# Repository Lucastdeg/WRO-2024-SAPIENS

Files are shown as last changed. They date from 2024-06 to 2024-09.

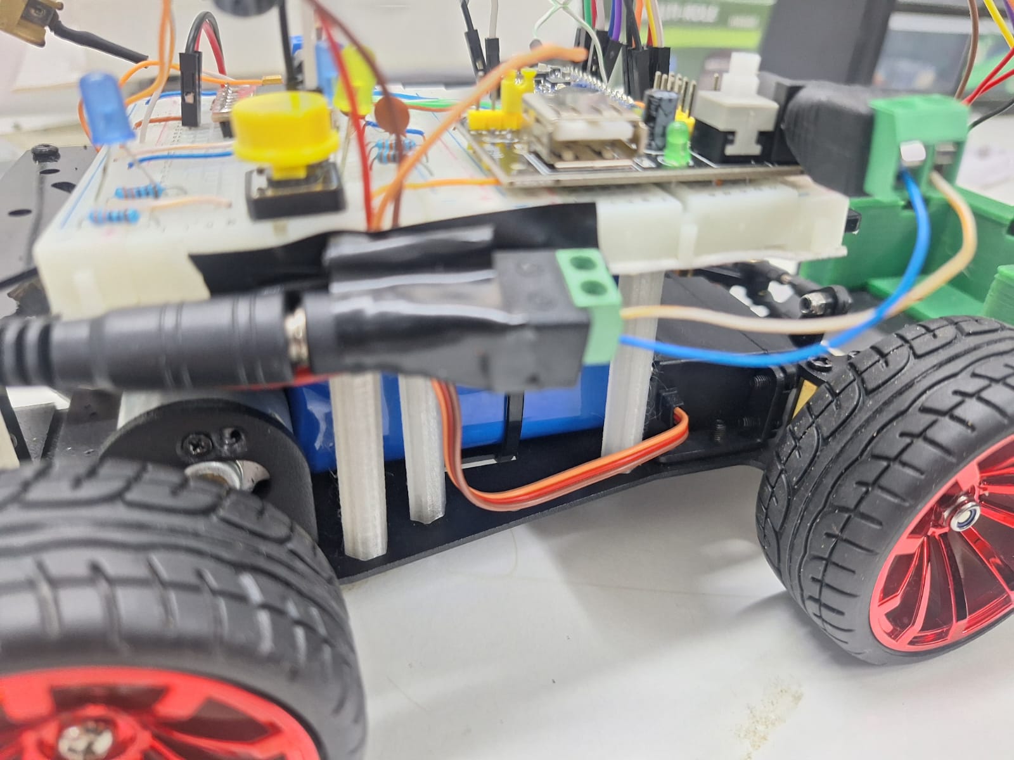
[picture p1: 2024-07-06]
v-photos/Electromechanical_Components/Battery Connection to circuit (Male Outing).jpeg

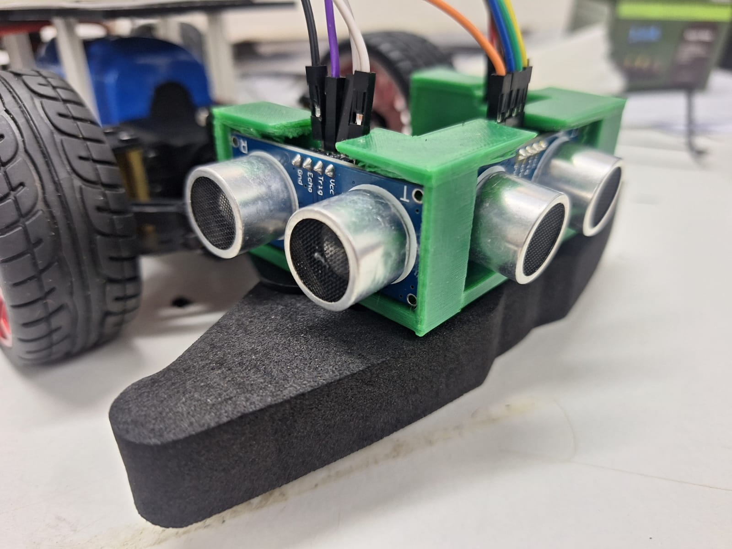
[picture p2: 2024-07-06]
v-photos/Electromechanical_Components/The Ultrasonic Sensors.jpeg

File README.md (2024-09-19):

# WRO-2024-SAPIENS
WRO-2024-SAPIENS

## Engineering Materials
All the materials used to create our robot
- 1 Arduino Nano Every (https://docs.arduino.cc/hardware/nano-every/)
- 1 TB6612 H-Bridge (HW-166)
- 4 Ultrasonic Sensors (1 at the front, 1 at the back, the other two right and left)
- 1 Small on/off switch
- 1 PushButton
- 1 Blue LEDS (1 for power, one for indication of the code)
- 2 resistors (360 Ohms) for code Indicator LEDS
- 25 Proto Wires
- 34 Rigid Wires (Hand cut)
- 2 Big Rigid Wires
- 2 Ceramic Capacitor 104
- 1 Capacitor 100 25-50V
- 1 Voltage Regulator L7805
- 1 Mini Power Supply HW-131 (Also works as voltage regulator) 5V and 3.3V2
- 1 Porta Fusibles
- 12V Battery 3S (18650 + BMS + 2 cable outings) (more about this can be seen in the electromehcanical components)
- 1 Chasis (DC Auto) This includes:
    - 4 Wheels
    - 1 Motor (more about this explained in other sections)
    - 1 Servo
- Multiple 3d pieces whih can be found in the following directory
[3d_files](models/3D_files/)



## Building instructions
- Chasis (Motors and base): https://mp.weixin.qq.com/s/dOADMsXeo7Lxebgg0yiY5Q
- Electronics (Circuit and battery): [The circuit diagram can be found in the schemes directory](schemes/)
- Code (For the arduino): [The source code can be found in the src directory](src/)

## Contents
- [Models](models/) This directory contains all used 3d models
- [Other](other/) This directory is empty for now, as no miscellancious files have had to be added
- [Process](process/) This directory will be completed for the national as it will contain the process that it took for us to get there
- [Schemes](schemes/) All wiring diagrams can be found in this directory
- [Source Code](src/) This directory contains all the code used in this proyect
- [Team Photos](t-photos/) The official Team photos can be found here
- [Performance Videos](p-videos/) The robot Performance videos for each challenge
- [Vehicle Pictures](v-photos/) All vehicle photos can be found in this directory, including some individual components
This is just a test to see if content linking works

## Introduction
Brief intro on our solution

For our robotics competition, we developed an innovative navigation solution that leverages Arduino's vision capabilities to detect and respond to color signals. By utilizing a camera module, our robot can identify green and red colors, which dictate its turning directions—left for green and right for red. This color-based navigation system is complemented by a comprehensive obstacle detection and avoidance mechanism.

To enhance our robot's awareness and maneuverability, we integrated four ultrasonic sensors—three positioned at the front and one at the back. These sensors provide real-time distance measurements, enabling the robot to detect and avoid obstacles from multiple directions. Our approach demonstrates the synergy of vision technology, ultrasonic sensing, and precise control algorithms, resulting in a responsive and reliable robotic solution.



## Mobility 
Our robot uses an Ackerman steering system, with this steering system we can make our robot do the turns that have to be done during the 3 rounds. But because of the shape of our chassis and the type of steering system we use, our robot can only turn up to a certain point. In the case of turning to the right, it can only turn 30 degrees and in the left one it can only turn 10 degrees.

Here you can see the shape of the chassis of our robot as a guide:
- [Chassis of our robot](v-photos/) 



Some of the problems we faced with the steering system is that we had to come up with a way for the robot to make the turns neither too tight nor too wide, to fix this we use ultrasonic sensors on the front, right and left side of the front of the robot that are detecting how far it started and how many degrees it has to move forward while it is turning. For example during the open challenge round we made the robot turn when one of the ultrasonic sensors on one of the sides stops detecting or detects a greater distance than it had detected during the straight line, the sensor that performs this action depends on whether it is the one on the right or left, when it is the one on the right is when the round is being performed clockwise and when it is the one on the left when it is counterclockwise. 

Meanwhile the servo motor is at 80 degrees the robot will turn to the left, so if it is at 120 degrees the robot will turn to the right, but you think that when the servo motor is at 100 degrees it will be in a position in which the wheels will be straight, this thought is incorrect because when the servo is at 100 degrees it will be slightly turning to the right, then we ask two questions, the first one is: So how many degrees should be the servo motor so that the robot wheels are straight? To answer this question, the degrees that the servo must be at for the wheels to be straight is 90 degrees, and this is where the second question comes in, which is: Why when the servo is at 90 degrees will the wheels be straight, if when the servo was at 80 degrees the robot would turn to the left and when the servo was at 120 degrees the robot would turn to the right, if the degrees that are in between these two numbers of degrees are 100 degrees? Well to answer this question, the 90 degree position is considered "straight" or "neutral" in many servo motor systems because it is the preconfigured standard in many servos to indicate that there is no deviation to the left or right and because of how we have the servo positioned with the chassis we are using and the Ackerman steering system our steering only goes from 80 to 120 degrees.

For the speed management part, our robot is generally going to go at 120 speed on straight lines, while it is rotating it will go at 100 of speed.

As for the equations we use 2 formulas, between the 2 formulas we have the turning time, this establishes that the speed that we are using during the turn, that is 100 We are going to divide it by 100 and the result we are going to multiply it by 1200 and this would give us the time during which we are going to rotate in milliseconds; the second formula is about the angle of rotation in this we are going to divide the speed by the result of the previous formula, then this result we are going to multiply it by 130 and the result that this formula gives us we are going to subtract it to another 130 and the result of this subtraction is going to give us the angle with which we are going to rotate. We use these formulas to make the turns between sections. 

## Strategy
Strategy Explanation
Color Detection with Arduino:
We integrated a Nicla vision with the arduino nano every to accurately detect colors. This system allows the robot to recognize green and red colors, which serve as signals to turn left or right, respectively. By using a camera module and appropriate color detection algorithms, the robot can continuously monitor its environment and respond in real time.

Directional Decision Making:
Upon detecting the color green, the robot is programmed to turn left. Conversely, when red is detected, the robot turns right. This color-based decision-making process ensures that the robot navigates efficiently and avoids obstacles or follows a designated path based on the predefined color signals.

Border Detection and Turning:
In addition to color detection, our robot is equipped with ultrasonic sensors to identify when and where it should turn. It uses an "umbral" which is a certain distance which if the robot pases, it will start to turn to a certain direction. That direction is decided by the other two ultrasonic sensors to the left and to the right.

Implementation Details
Code and Integration:
Our code, available here, outlines the specific algorithms and logic used for color detection, decision-making, and obstacle avoidance. The integration of the vision system with Arduino's control mechanisms is crucial for the robot's functionality.

Color Detection Algorithm:
The algorithm processes the camera feed to identify the presence of green or red. This involves filtering the image to isolate these colors and then using thresholding techniques to determine the direction.



Obstacle Avoidance Routine:
When the sensors detect an obstacle, the robot executes a series of steps to navigate around it. This includes stopping, scanning the surroundings, calculating an alternate path, and resuming its movement while continuing to rely on the color signals for direction.

Conclusion
Our solution leverages the capabilities of Arduino's vision system to create a responsive and efficient navigation strategy. By combining color detection with obstacle avoidance, our robot can intelligently navigate its environment, making it well-suited for the challenges of the competition.

This approach not only demonstrates the effectiveness of integrating vision with control systems but also highlights the importance of robust algorithms in achieving reliable performance in dynamic conditions.

## Code Explanation
In order to enact our strategy and enable our robot to complete each phase, our team created multiple programs that will be summarized and explained in the following text. For reference look at the [src directory](src).

The src directory is divided into 3 sections, Arduino Code, Nicla Code, and Other. This text will focus on the Arduino code as the Nicla is currently not being used. [The Arduino Code Directory](src/Arduino Code/) is divided in 2 sections, phase 1 and phase 2. At the time of writing, only phase 1 has been completed, that being said, our proyect is still in development, and in the near future it will be added to the github. 

[Phase 1](src/Arduino_Code/Phase_1):
Phase 1 contains multiple programs to show how our code has changed, the main code is called newcodephase1

- The program starts by defining all variables and importing all libraries, this include, all pins (except the two Led indicators), the max angle for the servo, and some other useful variables.

- Next is the PD, or Proportional Derivative. This PD is used later in "Accelerar Recto" to help mantain the robot in a straight line, there are multiple comments in the code explaining the PD, so the specific details will not be mentioned in this text. 

- After this comes the set up function, which as is said in the name, sets up the robot. It defines all pin modes and the servo. 

- Then comes the actual main part of the code, which can be found in the loop function. The loop function starts with a while loop that will repeat until a button is pressed. Pin #5 is in mode Input, which means that it recieves current. When the button is pressed, current from the battery is passed into the pin which causes the while loop to end. After the while loop ends, the 3 ultrasonic sensors measure the current distance, and each value is defined in a variable. This is done by calling the "medir_distancia" function which returns a float value.
  
- The medir distancia function can be found in line 241, it uses "cases" to determine which ultrasonic has to be activated. Once that is defined, the ultrasonic sends the sound waves and a duration value is returned, this value is processed by using the formula ((duration * 0.034 / 2)*0.95), which returns a distance reading in centimeters.

- Returning to the loop function, next up, a for loop starts. This for loop repeats 70 times, which is an absurd number of times right? Well thats the amount of times the function we use has to repeat in order to complete the 3 laps. Unfortunately, this is due to a weird error in our code that makes it so sometimes the turn function ends prematurely. 70 loops garantues that the robot completes the 3 laps, but in exchange, sometimes it does 3.5 or 4 laps, which means we can't consistently stop in the initial spot (this subtracts 3 points from our phase 1 score)

- Getting back to the functions used, first_turn is the function used for all turns, it was supposed to be only a function for the first turn, but it was so consistent we just used it repeatedly. First_turn is made up of 2 main parts, moving the robot forwards until it meets the umbral (or the left/right sensor detect more than 150 cms which indicated a turn), and then the actual turning.
- When the robot goes forward our pd constantly corrects the robot's position, we also have save crash function which makes it so if the robot is about to crash, it goes backwards and turns, preventing it from ending the round. This repeats until, how we mentioned earlier, the ultrasonic sensors forwards and back match the umbral or the right/left sensors detect more than 150 cms. It should probably be noted that the left anf right sensors almost never end the loop, and it is almost always the umbral.
- After the forwards loop ends, the robot detects right and left to decide what direction it will turn, the function left_turn and right_turn take in 2 parameters. Angle and time, angle being the angle at which it will turn, and time being the amount of time it will turn. Yet, if you see the actual code, you will notice that we set time at 0, so that means it shouldn't be turning right? Well, we found out that turning bya time was very inconsistent since gradual errors make the robot eventually crash, for this reason we are now using the left_end_turn function, which is incredibly consistent for 2 main reasons
- 1. It turns gradually from the specified angle (normally 60) to 84, increasing 1 degree every 112 miliseconds
  2. It turns, not by time, but until the ultrasonic sensors detect from a range of 100 to 30. This is the main reason why the robot is so consistent when turning compared to the previous code. Before, some very small errors could lead to crashes by the second lap, but with this code, we decrease the effect of those small errors substantially, since every turn will always be mostly straight, no matter at what angle it starts.

 - When the for loop ends, the breaking function (whichs stops the robot) sets in and the robot stops.

[Phase 2](src/):
Phase 2 consists of two different programs, one for the arduino nano every, and one for the nicla vision. Check each of their respective directories to see the code. The code for the nicla vision will be covered first, it focuses primarily on the color detection, but it also has the necessary integration modules to pass the information onto the nano every.

First of all let's cover the integration:
- The integration uses the wire library to connect the Nicla Vision and Nano every. It connects them bya I2C, or SCl and SDA connection. In both programs, the baudrate is set to 100000 and the address is set to the number 8. In the code it can be seen how the Nicla Vision is set to be the slave, this means that the nicla vision will send information to the nano every when it is called, if it was the other way around (like it previously was) the nano every would be called by the nicla vision.

Next is the color detection:
- The nicla vision will send 0 to the arduino nano every if it is green and 1 if it is red. It detects the colors by using the blob function integrated into openmv. The blob function contains parameters to define the sensitivity of the detection. It is based on the pixel count, the pixel area count and the intensity of the color. Two lists of different types of green and red are supplied to the function so that the camera can identify the color it is looking for. To determine the color that is going to be sent, the areas of all the detected blobs are added for red and for green. The one with the largest amount of area (the biggest amount of pixels) is the one the robot detects. Now, sometimes there will be no blocks in front of the robot, to detect this, we set a lower boundary of around 400 pixels, so if the total area is less than 400, no colors will be sent back to the robot.

Now, how do we utilize the 0s and 1s that we will recieve from the nicla vision?
For that we need to undertsand the arduino nano every's code:
- The code for phase 2 is vaguely based off of the code for phase 1, it uses a similar turn that measures the length of both ultrasonic sensors, the difference is it has an initial turn based on time. Besides from that it uses 2 functions to dodge left and right based on the readings of ultrasonic sensors. Before that though, it has to detect the color thats in front of the robot, it does this by calling the nicla vision and defining a variable as 0 or 1, (if there is no color it gets defined as 2). Then it dodges left or right depending on the reading and after that it will start going in alternating directions, by that it means if it detects red initially, it will go green next, and then red, alternating (as this pattern will always be present).

- This repeats until the robot crashes as we unfortunately, did not have time to do phase 3.

## Electromechanical Components
A lithium battery pack is being used in 3S1P configuration where 2 batteries are in parallel and then this pack is in series with the 2 batteries, to give a total of 12.6 Volts with 1900mAh capacity, together with the help of a BMS to manage the power input and output.
From this battery pack we are getting two cables, of which one has a male terminal and the other has a female terminal.

4 ultrasonic arduino sensors HC-SRO4 are being used. This sensor provides 2cm to 400cm of non-contact measurement functionality with a ranging accuracy that can reach up to 3mm. Each HC-SR04 module includes an ultrasonic transmitter, a receiver and a control circuit. There are only four pins that you need to worry about on the HC-SR04: VCC (Power), Trig (Trigger), Echo (Receive), and GND (Ground).

We used a Nicla Vision to detect the color of the obstacles, we made an algorithm to give the robot the ability to differentiate between green and red. 
We connected the Nicla Vision with the Arduino Nano Every through the SCL and SDA signals. 
When the Nicla Vision passes the information to the arduino about the color of the obstacle the arduino processes it and decides to turn left or right depending on whether the obstacle is red or green. 

Here is how the components are connected:
- [Wiring Diagrams](schemes/)

Unfortunately the Nicla Vision we used could not be found or obtained in the application we used for this reason we could not include it in the wiring diagram. But here is how the Nicla Vision is connected to the Arduino Nano Every:
-SDA from the Nicla Vision to pin D18 (SDA) of the Nano Every.
-SCL from the Nicla Vision to the D19 pin (SCL) of the Nano Every
-GND from the Nicla Vision to GND of the Nano Every
-VIN from the Nicla Vision to the 5V+ pin of the Nano Every

Here are some pictures of the batteries and sensors that we use: 
- [Batteries](v-photos/Electromechanical_Components/)

## Power Management
The battery power is separated in two parts. 
One part feeds the Arduino Nano Every and the Ultrasonic Sensors with 5 volts. This part make use of the Mini Power Supply HW-131 to regulate the voltage. 
The other part feeds the H-Bride TB6612 with 12 volts. 
Of course, all grounds are connected, but the 12 volts are only supplied in one positive line, this is the line that feeds the H-Bridge. 
Yet, this line connects to another positive line, but with the L7805 voltage regulator. This voltage regulator ensures that the servo and the power LED get 5 volts. Finally, the servo uses a capacitor to store energy in the case that the current demand is too high.

""Note: We use a porta fusible for safety of a short circuit in the 12 volts outing. It is highly recomended that this is used as this lithium battery could lead to a very dangerous safety hazard if not managed carefully. 

- [You can see the vehicle picture for reference](v-photos/)

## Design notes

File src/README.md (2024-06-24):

# Source Code
This directory contains all the code used for our completion of the 2024 Future Engineers challenge

It is separated into three main directories:
Arduino Code - contains the code used for the arduino nano every
Nicla Vision Code - contains the code used for the nicla vision
Other - miscellaneous programs used for the development of our solution (such as the PID simulator created using python)

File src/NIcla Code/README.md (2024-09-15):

# Nicla Vision Code

The code is explained in the main readme file. 

Just for you though, Ill vaguely explain it here as well
The code consists of one main function and inside of that there are multiple functions

- cameraConfig is a higher order function that sets up the camera and takes a picture 
- •	find_color_blobs gets the amount of pixels in a all color blobs and sends back 0 for green or 1 for red, depending on how many pixels are found for each color.
- Send info simply sends a value, (0 or 1) to the specified address
- I recommend greatly that you look at the code, there are multiple comments that get into more detail on the integration

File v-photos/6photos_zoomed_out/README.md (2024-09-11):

# 6 Photos

These photos include the nicla vision and some other minor change that were made to the robot
- Ultrasonic sensor in the back
- The new cables for the battery connection
- Changed position of capacitator
- Nicla Vision (disconnected)
- Changed Blue Led
- New button
- Not using Tape for 5v outing anymore
- New Servo
- New ultrasonic sensors
- Foam at front to protect robot from crashes

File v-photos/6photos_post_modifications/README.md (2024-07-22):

# Vehicle Pictures Post Modifications

While practicing over the week our team encountered multiple problems
1. The rigid cables were burnt and were not transmitting voltage/current well
2. The on/off switch had the same problem (although the reason is still only a theory)
3. The Battery was not charging
4. The Voltage regulator was not working

Due to this we had to change multiple things on the robot that can be seen in the new pictures

- We changed the battery so you might notice there are different cables for the battery now (the zip tie is also different)
- We changed the rigid cables to thicker bigger cables that could handle more voltage/current
- We replaced the voltage regulator
- We changed the on/off switch (you can see the zip tie is different)

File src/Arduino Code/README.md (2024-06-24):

# Arduino Code

All the code used for the arduino nano every
Contains:
Mention contents

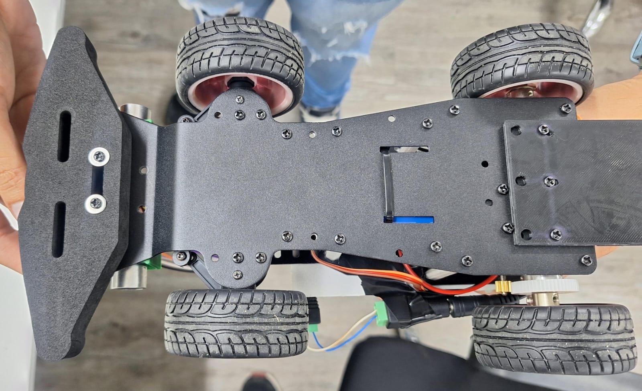
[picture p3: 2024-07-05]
v-photos/6photos_pre_modifications/Bottom View.jpeg

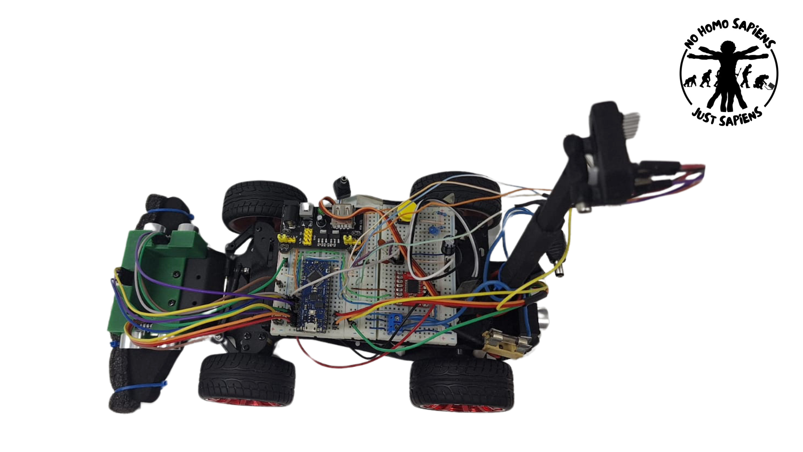
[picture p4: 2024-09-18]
v-photos/Current_v_photos/topside.png

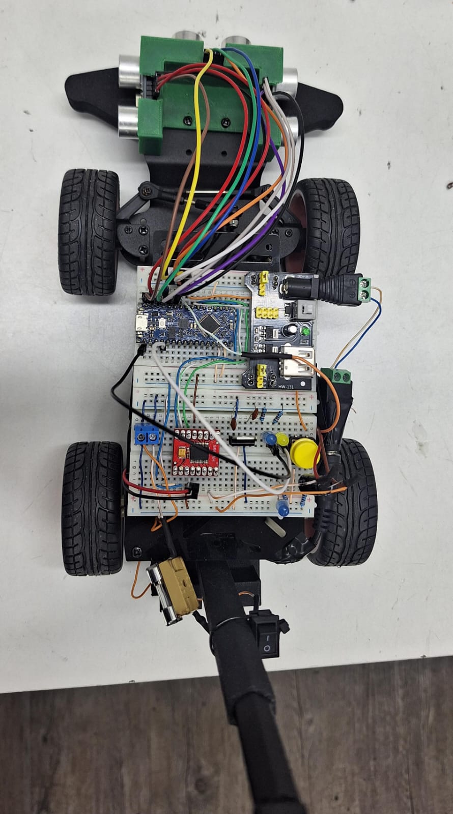
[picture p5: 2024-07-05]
v-photos/6photos_pre_modifications/Top View.jpeg

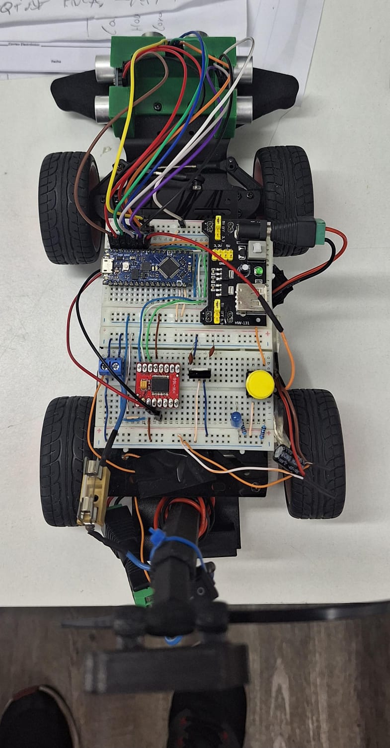
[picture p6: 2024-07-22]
v-photos/6photos_post_modifications/Top Side.jpeg

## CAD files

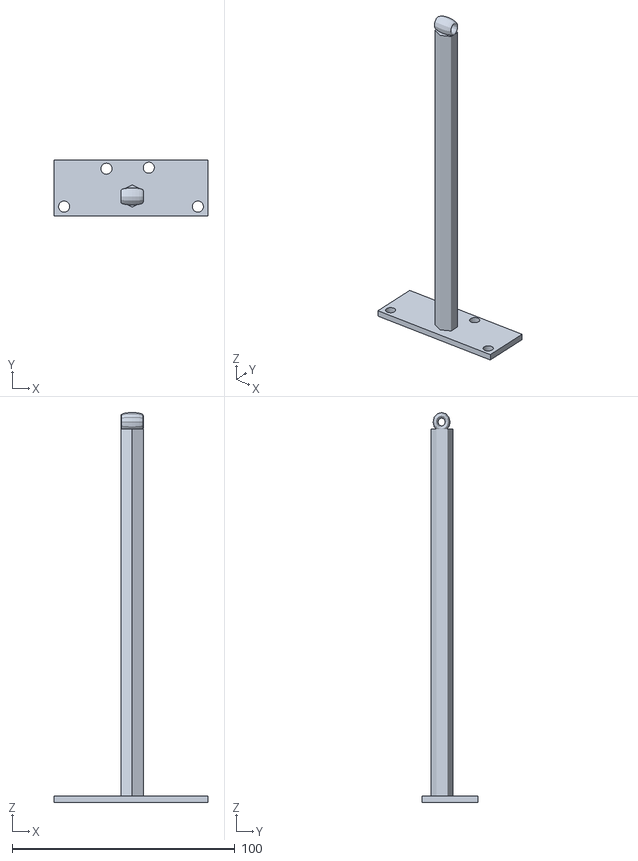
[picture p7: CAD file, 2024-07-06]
models/3D_files/soporte_nicla_solo_base_no_ultra.stl
69.0 x 25.0 x 175.0

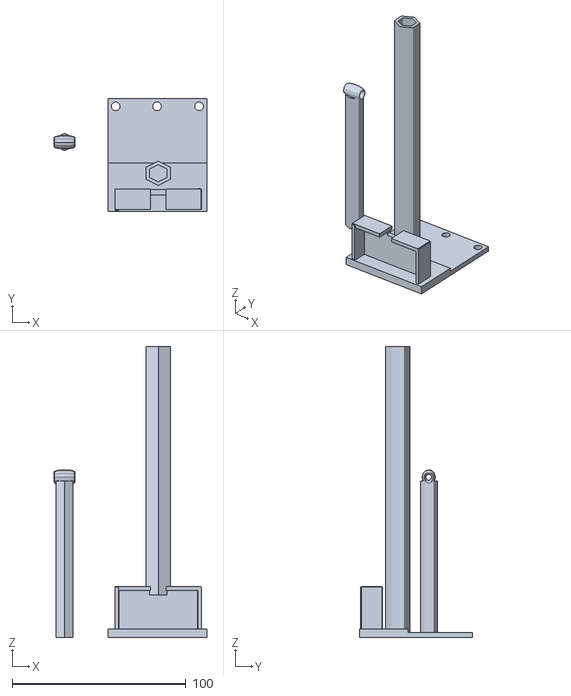
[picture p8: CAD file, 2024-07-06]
models/3D_files/soporte_trasero+ultrasonico.stl
88.0 x 65.0 x 167.5

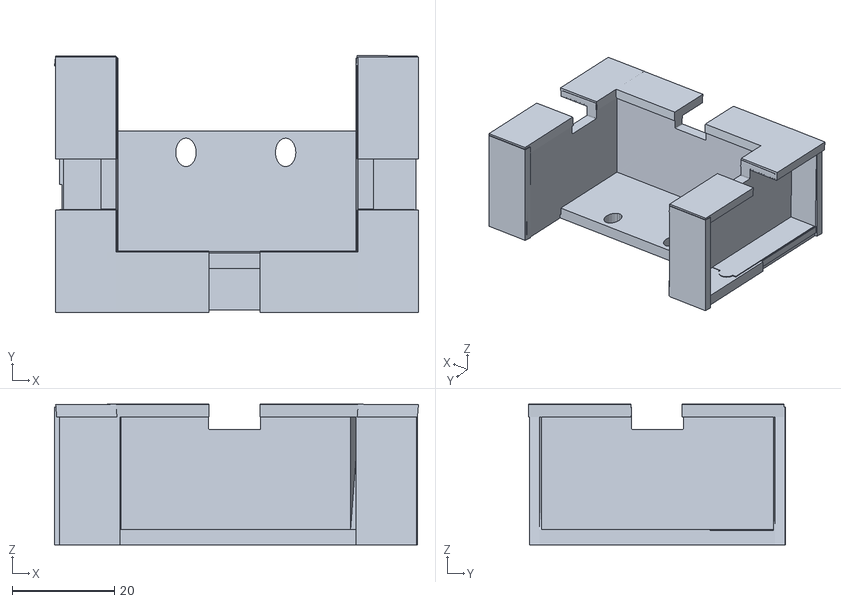
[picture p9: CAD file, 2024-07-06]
models/3D_files/soporte_delantero_4_ultrasonico.stl
71.2 x 50.2 x 27.5

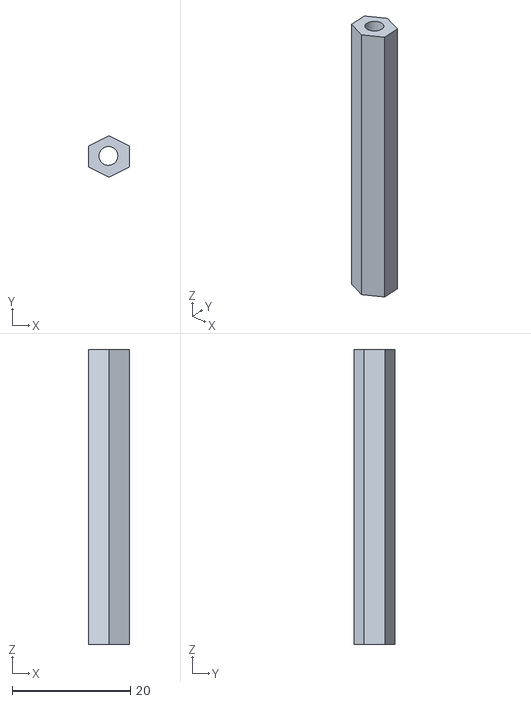
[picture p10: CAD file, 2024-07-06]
models/3D_files/Barilla_elevadora.stl
7.00 x 7.00 x 50.0

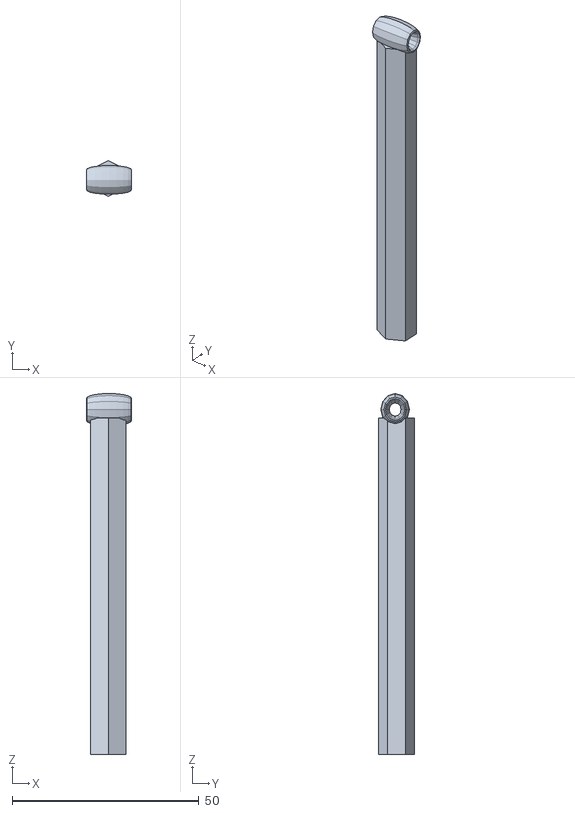
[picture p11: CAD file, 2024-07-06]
models/3D_files/barra_soporte_nicla_sola.stl
12.0 x 9.60 x 96.6

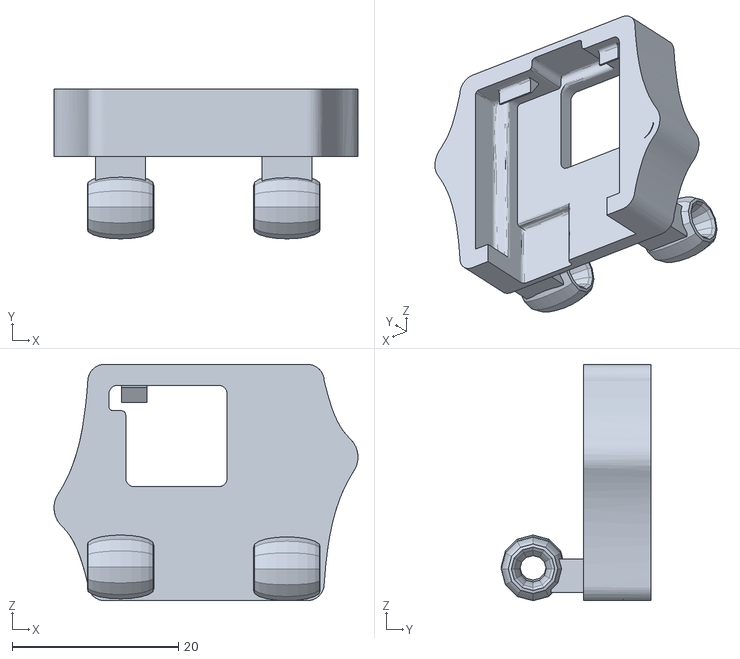
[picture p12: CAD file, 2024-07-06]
models/3D_files/Nicla_case.stl
36.5 x 18.0 x 28.4

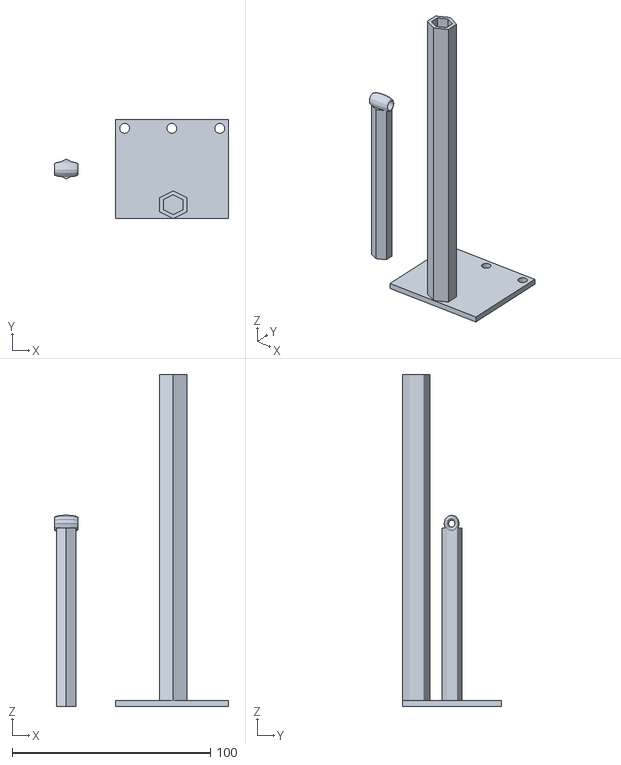
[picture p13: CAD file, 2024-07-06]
models/3D_files/base_nicla_barra_no_ultrasonico.stl
88.0 x 50.0 x 167.5

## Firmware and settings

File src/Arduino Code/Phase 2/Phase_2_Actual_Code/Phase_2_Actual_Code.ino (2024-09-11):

#include <Servo.h>
#include <Wire.h>

//const int delay_uni = 200;
//I2C:
const int i2c_dir = 8;
const int BUFFER_SIZE = 1; // Tamaño del buffer para almacenar los datos recibidos
int receivedData[BUFFER_SIZE];
bool go = false;

float R_tem;
float L_tem;

bool first_forwards = true;

bool turn_direction;
bool startsred = true;

int col = 2;

int count_laps = 0;
//Ultrasonic pins:
const int ultra_R_echo = 7;
const int ultra_R_trig = 8;

const int ultra_F_echo = 9;
const int ultra_F_trig = 10;

const int ultra_L_echo = 11;
const int ultra_L_trig = 12;

const int ultra_B_echo = 13;
const int ultra_B_trig = 14;

unsigned long time_a, time_b, time_c, time_d;

//Motor pins:
const int IN1 = 2;  //AIN1
const int ENA = 3;  // PWMA
const int IN2 = 4;  //AIN2

//Steering servo pin:
int max_R_angle = 125; //max giro R
int max_L_angle = 67; //max giro L
Servo myservo;
const int servo_pin = 6;

// Defining class for PD regulation
class Regulator {
public:
  // Defining parameterized constructor with Kp, Kd, and Target (The target distance between walls) as parameters
  Regulator(float kp, float kd, float target, int stationary)
    : Kp(kp), Kd(kd), Target(target), Stationary(stationary), Pre_ErrorR(0), Pre_ErrorL(0) {} // Defining all the parameters we will use for the steer

  // Actual Function that will return the steer for the robot
  float Steer(float Distance_R, float Distance_L){

    // Proportional Error
    float errorR = Distance_R - Distance_L;

    // Derivative Error
    float derivativeR = errorR - Pre_ErrorR;

    // PD for Right Sensor
    float R_Correction = Kp * errorR + Kd * derivativeR;

    // PD for Left Sensor

    float F_Correction = R_Correction;
    // The bigger the distance right the more it should turn right, thats why we subtract the (-)R_Correction to the 90
    // Meanwhile if the distance to the left was real big, it means we have to add subtract the 90, which is why we add (-)L_Correction

    if (F_Correction > 0){
      F_Correction = pow(F_Correction, 1.05);
    }
    
    // Defining final servo position
    float Servo_Pos = Stationary + F_Correction;
    // 90 is the where it should stay

    if (Servo_Pos < 70){
      Servo_Pos = 70;
    }
    else if (Servo_Pos > 120){
      Servo_Pos = 120;
    }

    // Although the Kp and Kd are designed to limit the Servo to a range of 60-120 degrees, the Derivative can increase enough to nullify that, for this reason we add a cut off

    return Servo_Pos;
  }

private:
  float Kp;
  float Kd;
  float Target;
  int Stationary;

  float Pre_ErrorR;
  float Pre_ErrorL;
};

void setup() {
  //Comunication setup:
  //Comunication setup:
  Serial.begin(100000);
  Wire.begin();
  pinMode(5, INPUT);

  //motor pin setup:
  for(int i = 2; i<5; i++){
    pinMode(i, OUTPUT);
  }

  //ultrasonic pins setup:
  for (int i = 7; i < 15; i++){
    if(i % 2 == 0) pinMode(i, OUTPUT);
    else pinMode(i, INPUT);
  }  

  //light indicators
  //pinMode(13, OUTPUT);
  //pinMode(14, OUTPUT);

  //Steering servo setup:
  myservo.attach(servo_pin);
  myservo.write(87);
  delay(500);
}


void loop() {

  while(go == false){
    if(digitalRead(5)) go = true;
    delay(100);
  }

  float dis_F_inic = medir_distancia('F');
  //float dis_R_inicial = medir_distancia('R');
  //float dis_L_inicial = medir_distancia('L');

  //delay(100);


  // 1 if red 0 if green
  if (dis_F_inic > 130){
    col = 2;
  }else{
    col = receiveColor();
  }
 

  // First check that gets direction and dodges in case of immeadite obstacle
  if (first_forwards) {
    first_dodge(col);
  } 

  if (startsred and turn_direction) {
    left_turn_end(130, 60, 950);
    align_back(120, 80);

  }
  if (startsred and !turn_direction) {
    left_turn_end(130, 125, 950);
    align_back(120, 80);

  }
  col = receiveColor();


  digitalWrite(IN1, LOW);
  digitalWrite(IN2, LOW);
  analogWrite(ENA, 0);
  delay(10000);
  //go = false;

}

void align_back(int v, int umbral) {
  float temp_back = medir_distancia('B');
  while(temp_back > umbral) {
    digitalWrite(IN1, LOW);
    digitalWrite(IN2, HIGH);
    analogWrite(ENA, v);
    delay(20);
    temp_back = medir_distancia('B');
  }
}


void first_dodge(int color) {

  if (color == 1) { // red
    dodge_right(128, 80, 900, 18);
    startsred = true;

  } else if (color == 0) {
    dodge_left(128, 80, 800, 18);
    startsred = false;
    
  } else {
    float dis_F_tem = medir_distancia('F');

    while (dis_F_tem > 90) {
      digitalWrite(IN1, HIGH);
      digitalWrite(IN2, LOW);
      analogWrite(ENA, 130);
      delay(20);

      myservo.write(86);
      dis_F_tem = medir_distancia('F');
    }
    startsred = true; // let luck decide
      // move forwards and turn

  }
  float dis_R_inicial = medir_distancia('R');
  float dis_L_inicial = medir_distancia('L');

  if (dis_R_inicial > dis_L_inicial) {
    turn_direction = false;
  } else {
    turn_direction = true;
  }

  
  myservo.write(86);
}

float proportional_right(float kp, float target, int stationary) {
  float error;
  error = medir_distancia('R') - target;
  float returnval = stationary + (error*kp);
  
  if (returnval > 120){
    return 120;
  } else {
    return returnval;
  }


}

float proportional_left(float kp, float target, int stationary) {
  float error;
  error = medir_distancia('L') - target;

  float returnval = stationary - (error*kp);

  if (returnval < 70){
    return 70;
  } else {
    return returnval;
  }

}

void dodge_right(int v, int umbral1, int time, float target) {
  float dis_F_tem = medir_distancia('F');
  float dis_R_tem = medir_distancia('R');

  float count = time/20;

  while ((count > 0 and dis_R_tem > 10)) {
    digitalWrite(IN1, HIGH);
    digitalWrite(IN2, LOW);
    analogWrite(ENA, v+15);
    delay(20);

    myservo.write(proportional_right(0.8, target, 85));
    dis_R_tem = medir_distancia('R');
    dis_F_tem = medir_distancia('F');
    count = count-1;
  }
  myservo.write(75);
  while(dis_F_tem > umbral1) {
    digitalWrite(IN1, HIGH);
    digitalWrite(IN2, LOW);
    analogWrite(ENA, v+4);
    delay(20);
    dis_F_tem = medir_distancia('F');
  }

  myservo.write(86);
  digitalWrite(IN1, HIGH);
  digitalWrite(IN2, LOW);
  analogWrite(ENA, 0);

}


void dodge_left(int v, int umbral1, int time, float target) {
  float dis_F_tem = medir_distancia('F');
  float dis_L_tem = medir_distancia('L');

  float count = time/20;

  while ((count > 0 and dis_L_tem > 10)) {
    digitalWrite(IN1, HIGH);
    digitalWrite(IN2, LOW);
    analogWrite(ENA, v+15);
    delay(20);

    myservo.write(proportional_left(0.65, target, 85));
    dis_L_tem = medir_distancia('R');
    dis_F_tem = medir_distancia('F');
    count = count-1;
  }
  analogWrite(ENA, v+4);
  myservo.write(125);
  delay(350);
  while(dis_F_tem > umbral1) {
    digitalWrite(IN1, HIGH);
    digitalWrite(IN2, LOW);
    analogWrite(ENA, v+4);
    delay(20);
    dis_F_tem = medir_distancia('F');
  }

  myservo.write(86);
  digitalWrite(IN1, HIGH);
  digitalWrite(IN2, LOW);
  analogWrite(ENA, 0);

}




// FUNCTION TO USE DOWN HERE AND UP HERE

void left_turn_end(int v, int angle, int time) {

  myservo.write(angle);

  digitalWrite(IN1, HIGH);
  digitalWrite(IN2, LOW);
  analogWrite(ENA, v);
  delay(time);

  float R = medir_distancia('R');
  float L = medir_distancia('L');
  float add = R+L;

  while (add > 105 or add < 70) {
    digitalWrite(IN1, HIGH);
    digitalWrite(IN2, LOW);
    analogWrite(ENA, v);
    delay(112); // 120
    myservo.write(angle);
    angle = angle + 1;
    if (angle > 84) {
      angle = 84;
    }
    R = medir_distancia('R');
    L = medir_distancia('L');
    add = R+L;
    
  }

  myservo.write(angle);

  digitalWrite(IN1, HIGH);
  digitalWrite(IN2, LOW);
  analogWrite(ENA, v);
  delay(700);
  myservo.write(86);

}

void save_crash(int v) {
  float R = medir_distancia('R');
  if (R < 10) {
    digitalWrite(IN1, LOW);
    digitalWrite(IN2, HIGH);
    delay(1000);
    myservo.write(60);
    digitalWrite(IN1, HIGH);
    digitalWrite(IN2, LOW);
    delay(1300);
    myservo.write(86);
  }
}

void breaking(int time) {
  digitalWrite(IN1, LOW);
  digitalWrite(IN2, LOW);
  delay(time);
}

// I am only copy pasting to allow for more specifications later on, either way left turn is the main function
void right_turn(int v, int angle, int time) {
  float kp = 4;
  time = get_time(v, time, R_tem, L_tem, 4, turn_direction); // velocity, base time, right reading, left reading, kp the bigger the more effect

  myservo.write(angle);
  acelerar(v);
  delay(time);

  //right_turn_end(134, 125);

}

void right_turn_end(int v, int angle, int time) {

  myservo.write(angle);

  digitalWrite(IN1, HIGH);
  digitalWrite(IN2, LOW);
  analogWrite(ENA, v);
  delay(time);

  float R = medir_distancia('R');
  float L = medir_distancia('L');
  float add = R+L;

  while (add > 105 or add < 70) {
    digitalWrite(IN1, HIGH);
    digitalWrite(IN2, LOW);
    analogWrite(ENA, v);
    delay(112); // 120
    myservo.write(angle);
    angle = angle - 1;
    if (angle < 88) {
      angle = 88;
    }
    R = medir_distancia('R');
    L = medir_distancia('L');
    add = R+L;
    
  }

  myservo.write(angle);

  digitalWrite(IN1, HIGH);
  digitalWrite(IN2, LOW);
  analogWrite(ENA, v);
  delay(700);
  myservo.write(86);

}

float get_time(int v, int base_time, float R, float L, float kp, bool left) {
  int speed_mod = (100/v);
  float error;


  if (left) {
    error = L - R;
  }
  else {
    error = R - L;
  }

  return (base_time + (error*kp))*speed_mod;

}

void acelerar(int v){
  digitalWrite(IN1, HIGH);
  digitalWrite(IN2, LOW);
  analogWrite(ENA, v);
}


int receiveColor() {
  Wire.requestFrom(0x08, 1); // Request 1 byte from the Nicla Vision

  if (Wire.available()) {
    int colorData = Wire.read(); // Read the received data
    return colorData;
  } else {
    return -1; // Return -1 if no data received (indicates an error)
  }
}

float medir_distancia(char dir){
  int trig = 0;
  int echo = 0;
  switch(dir){
    case 'F':
      trig = ultra_F_trig;
      echo = ultra_F_echo;
      break;
    case 'R':
      trig = ultra_R_trig;
      echo = ultra_R_echo;
      break;
    case 'L':
      trig = ultra_L_trig;
      echo = ultra_L_echo;
      break;
    case 'B':
      trig = ultra_B_trig;
      echo = ultra_B_echo;
      break;
    default:
      return 0.0;
  }
  digitalWrite(trig, LOW);
  delayMicroseconds(2);
  digitalWrite(trig, HIGH);
  delayMicroseconds(10);
  digitalWrite(trig, LOW);
  long duration = pulseIn(echo, HIGH);
  float distance_cm = (duration*0.0343)/2;
  return distance_cm * 1; //change the 1 for any modification
}

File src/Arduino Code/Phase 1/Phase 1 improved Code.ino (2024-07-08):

#include <Servo.h>
#include <Wire.h>
const int delay_uni = 200;
//I2C:
const int i2c_dir = 8;
const int BUFFER_SIZE = 1; // Tamaño del buffer para almacenar los datos recibidos
int receivedData[BUFFER_SIZE];
bool go = false;

//Ultrasonic pins:
const int ultra_R_echo = 7;
const int ultra_R_trig = 8;

const int ultra_F_echo = 9;
const int ultra_F_trig = 10;

const int ultra_L_echo = 11;
const int ultra_L_trig = 12;

const int Light1 = 13;
const int Light2 = 14;

unsigned long time_a, time_b, time_c, time_d;

//Motor pins:
const int IN1 = 2;  //AIN1
const int ENA = 3;  // PWMA
const int IN2 = 4;  //AIN2

//Steering servo pin:
int max_R_angle = 125; //max giro R
int max_L_angle = 67; //max giro L
Servo myservo;
const int servo_pin = 6;

// Defining class for PD regulation
class Regulator {
public:
  // Defining parameterized constructor with Kp, Kd, and Target (The target distance between walls) as parameters
  Regulator(float kp, float kd, float target)
    : Kp(kp), Kd(kd), Target(target), Pre_ErrorR(0), Pre_ErrorL(0) {} // Defining all the parameters we will use for the steer

  // Actual Function that will return the steer for the robot
  float Steer(float Distance_R, float Distance_L){

    // Proportional Error
    float errorR = Target - Distance_R;
    float errorL = Target - Distance_L;

    // Derivative Error
    float derivativeR = errorR - Pre_ErrorR;
    float derivativeL = errorL - Pre_ErrorL;

    // PD for Right Sensor
    float R_Correction = Kp * errorR + Kd * derivativeR;

    // PD for Left Sensor
    float L_Correction = Kp * errorL + Kd * derivativeL;

    float F_Correction = L_Correction - R_Correction;
    // The bigger the distance right the more it should turn right, thats why we subtract the (-)R_Correction to the 90
    // Meanwhile if the distance to the left was real big, it means we have to add subtract the 90, which is why we add (-)L_Correction

    if (F_Correction > 0){
      F_Correction = pow(F_Correction, 1.1);
    }
    
    // Defining final servo position
    float Servo_Pos = 88 + F_Correction;
    // 90 is the where it should stay

    if (Servo_Pos < 70){
      Servo_Pos = 70;
    }
    else if (Servo_Pos > 120){
      Servo_Pos = 120;
    }

    // Although the Kp and Kd are designed to limit the Servo to a range of 80-120 degrees, the Derivative can increase enough to nullify that, for this reason we add a cut off

    return Servo_Pos;
  }

private:
  float Kp;
  float Kd;
  float Target;

  float Pre_ErrorR;
  float Pre_ErrorL;
};

void setup() {
  //Comunication setup:
  Serial.begin(115200);
  Wire.begin(i2c_dir);
  Wire.onReceive(receiveEvent);
  pinMode(5, INPUT);

  //motor pin setup:
  for(int i = 2; i<5; i++){
    pinMode(i, OUTPUT);
  }

  //ultrasonic pins setup:
  for (int i = 7; i < 13; i++){
    if(i % 2 == 0) pinMode(i, OUTPUT);
    else pinMode(i, INPUT);
  }  

  //light indicators
  pinMode(13, OUTPUT);
  pinMode(14, OUTPUT);

  //Steering servo setup:
  myservo.attach(servo_pin);
  myservo.write(80);
  delay(500);
}

void loop() {
  while(go == false){
    if(digitalRead(5)) go = true;
    delay(100);
  }

  float dis_F_inicial = medir_distancia('F');
  float dis_R_inicial = medir_distancia('R');
  float dis_L_inicial = medir_distancia('L');

  for(int i=0; i<12; i++){
    acelerar_recto(85, 120);
    auto_giro(100);
  }
  
  delay(500);
  go = false;
}

//Funciones:
void acelerar_recto(float umbral, int v){
  float dis_F_actual = medir_distancia('F');
  float dis_R_actual = medir_distancia('R');
  float dis_L_actual = medir_distancia('L');
  digitalWrite(Light1, HIGH);

  float dis_R_tem, dis_L_tem;

  // Here goes the Kp and Kd values with the target distance
  // Regulator regular(0.43, -0.07, 40);
  Regulator regular(0.15, -0.01, 40);

  while(dis_F_actual > umbral+8){
    digitalWrite(IN1, HIGH);
    digitalWrite(IN2, LOW);
    analogWrite(ENA, v);
    delay(20);
    dis_R_tem = medir_distancia('R');
    dis_L_tem = medir_distancia('L');

    // Mejorar correcion de posicion
    float posicion = regular.Steer(dis_R_tem, dis_L_tem);

    myservo.write(posicion);

    dis_F_actual = medir_distancia('F');

  } 
  digitalWrite(Light1, LOW);
  digitalWrite(IN1, LOW);
  digitalWrite(IN2, LOW);
  delay(delay_uni);
}

void acelerar(int v){
  digitalWrite(IN1, HIGH);
  digitalWrite(IN2, LOW);
  analogWrite(ENA, v);
}

void auto_giro(int v){
  float time = 1200 * (v/100);
  float angle;

  float dis_R_actual = medir_distancia('R');
  delay(5);
  float dis_L_actual = medir_distancia('L');
  delay(5);
  float dis_F_actual = medir_distancia('F');
  delay(5);
  digitalWrite(Light2, HIGH);
  if(dis_R_actual > dis_L_actual){
    float angle = max_R_angle - (max_R_angle * v/time);
    myservo.write(angle-5);
    delay(10);
  }
  else{
    float angle = max_L_angle - (max_L_angle * v/time);
    myservo.write(angle-5);
    delay(10);
  }
  acelerar(v);
  delay(time);
  myservo.write(91);
  delay(20);

  float dis_LAT_tem = medir_distancia('R') + medir_distancia('L');
  while(dis_LAT_tem < 120 and dis_LAT_tem > 80){
    myservo.write(84);
    delay(20);
    myservo.write(86);
    delay(20);
    dis_LAT_tem = medir_distancia('R') + medir_distancia('L');
  }
  digitalWrite(Light2, LOW);
  digitalWrite(IN1, LOW);
  digitalWrite(IN2, LOW);
  delay(10);
}

/*
void estacionarse(float dis_F, float dis_B){
  float dis_f_tem = dis_F / medir_distancia('F') - 10;
  delay(5);
  float dis_b_tem = dis_B / medir_distancia('B') - 10;
  delay(5);

  while(dis_f_tem < 1.2 and dis_f_tem > 0.8 or dis_b_tem > 1.2 and dis_b_tem < 0.8){
    acelerar(90);
    myservo.write(95);
    delay(20);
    myservo.write(85);
    delay(20);
    dis_f_tem = dis_F / medir_distancia('F') - 10;
    dis_b_tem = dis_B / medir_distancia('B') - 10;
  }
  stop();
}
*/

float medir_distancia(char dir){
  int trig = 0;
  int echo = 0;
  switch(dir){
    case 'F':
      trig = ultra_F_trig;
      echo = ultra_F_echo;
      break;
    case 'R':
      trig = ultra_R_trig;
      echo = ultra_R_echo;
      break;
    case 'L':
      trig = ultra_L_trig;
      echo = ultra_L_echo;
      break;
    default:
      return 0.0;
  }
  digitalWrite(trig, LOW);
  delayMicroseconds(2);
  digitalWrite(trig, HIGH);
  delayMicroseconds(10);
  digitalWrite(trig, LOW);
  long duration = pulseIn(echo, HIGH);
  float distance_cm = duration * 0.034 / 2;
  return distance_cm * 0.95;
}
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

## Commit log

2024-07-06 Added Arduino Code and changed Right Side Vehicle picture (it was blurry)
2024-07-06 Started adding engineering materials
2024-07-06 added all 3D_files
    bariila_estabilizadora
    barra_soporte_nicla
    ultrasonico
    nicla case
    base ultrasonico
    ultrasonico+soprte trasero
    [Barilla_elevadora.stl, Nicla_case.stl, barra_soporte_nicla_sola.stl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]
2024-07-06 Added more engineering materials
2024-07-06 Finished adding engineering materials
2024-07-06 Added power description
2024-07-08 Added instructions for how to create the robot
    Added chassis creation video, then linked the schemes directory, and also linked the code
2024-07-09 Added information about the mobility management
    Added the information about the mobility management, this include an explanation of our steering system and some of the equations that we use
2024-07-09 Added the wiring diagram
    Added the wiring diagram document and a image of it
    [Wiring Diagram.fzz]
2024-07-22 Changed materials
    Added the two big rigid wires used for the connection
2024-07-30 Changed materials
    Added fourth ultrasonic sensor
2024-08-03 Update the Materials
    In this commit I makes some updates of the materials that we used on our robot
2024-08-06 Update of the Wiring Diagram
    Here is an updated version of the wiring diagrams that we have
    [Wiring Diagram.fzz]
2024-08-06 Update of The wiring diagram on the electromchanical Componentes
    In this update I add how the Nicla Vision is connected with the Arduino Nano every
2024-09-11 Phase 2 explanation arduino nano every
2024-09-18 wiring diagram
    labeled
2024-09-18 Update Wiring Diagram.png
2024-09-18 current photos
2024-09-25 La que esta funcionando en este momento
    Juezes si ustedes leen esto, este codigo se hiso en horas de desesperacion
    Estoy abierto a cualquier preguntas sobre la etica de este codigo
